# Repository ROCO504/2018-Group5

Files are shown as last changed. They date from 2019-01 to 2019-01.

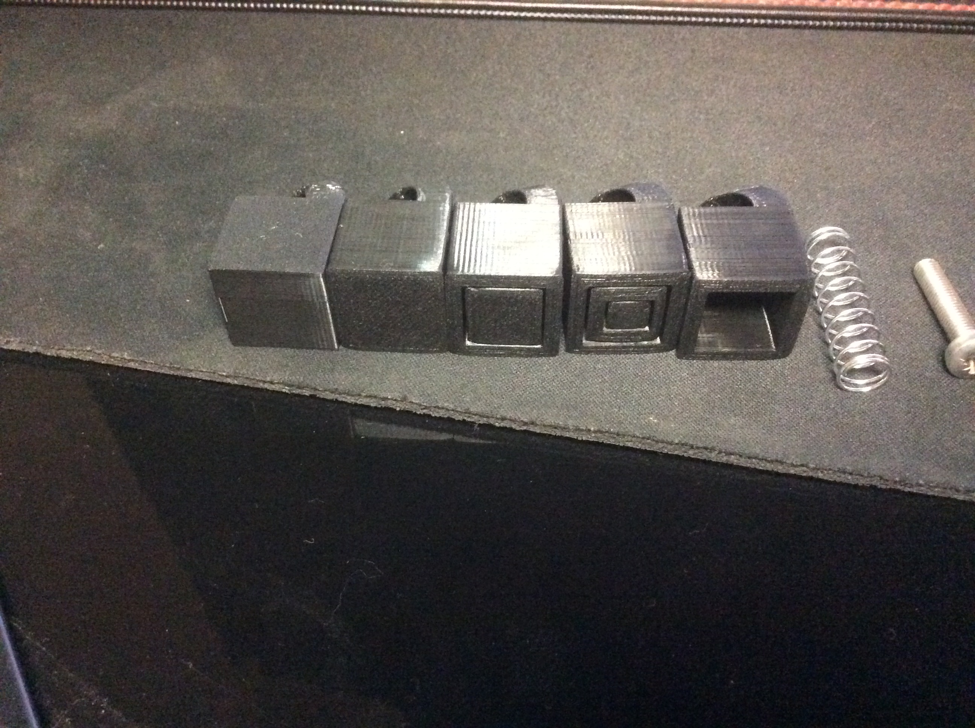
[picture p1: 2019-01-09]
Pictures/Test Cubes.JPG

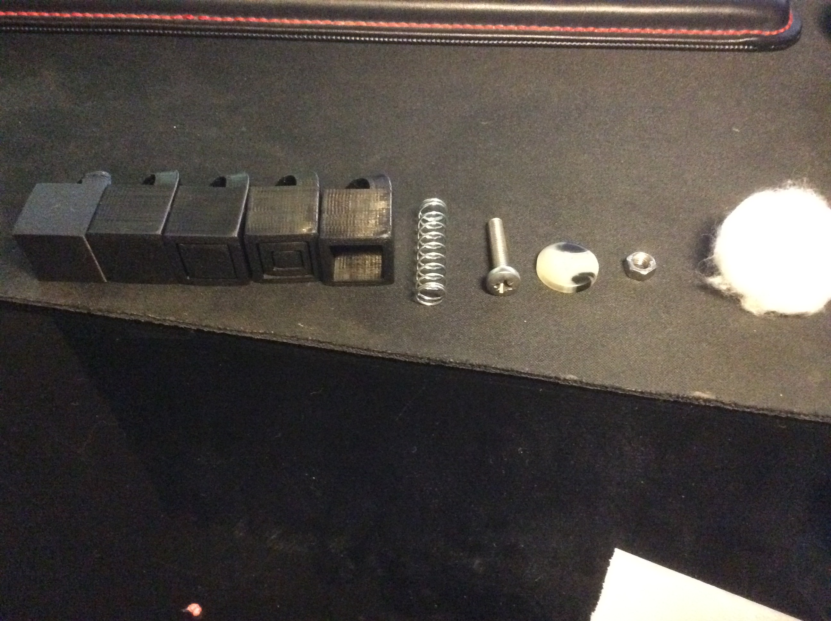
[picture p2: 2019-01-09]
Pictures/All Test parts.JPG

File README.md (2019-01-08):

ROCO504 Group 5 Readme File

Robotic Jamming gripper Hand Repository

This is a repository created for the Roco 504 module at Plymouth University in the school of Computing, Electronics and Mathematics. The code, design files and additional folders are created specifically for this project. The code is developed to be used on an Arduino Mega 2560 using 4 potentionmeters to control the digit position. 

The code is a simple digit control as the majority of this project was research based looking at the limits of using the jamming transition for grip strength

The FEA is adapted from the early design work and guided the itterations of rapid prototyping

Tensile Testing Data was gathered in the Smeaton Materials Lab.

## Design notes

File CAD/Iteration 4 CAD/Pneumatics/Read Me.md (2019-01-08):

A Store for CAD Files for parts relating to the air systems

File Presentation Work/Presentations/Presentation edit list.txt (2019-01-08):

Slide 1 TITLE
Slide 2 Why
	Hybrid/Soft/Hard
	Explain pros/cons of each
Slide 3 Project progress
	Start from comparing hard grippers, hands and human hand
Slide 4 Design key structure
	Break down into parts
		-Digit
		-Base
		-Pneumatics
			-Air vs water
			-Filter
		-Electronics
		-Code
Slide 5 Design Progression
	Digit Iterations
	Base Iterations
	Code Iterations
Slide 6 Electronic Progression
	Compare the motor strengths
Slide 7 Project Development
	Talk through what went right/wrong
Slide 8 Numerical Data of testing jamming
	Testing of different granuals vs journal articles
Slide 9 Overall design at presentation
	Picture talk about what it does

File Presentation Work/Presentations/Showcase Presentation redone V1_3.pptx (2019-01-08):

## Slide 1

Soft Jamming Robotic Gripper
An alternative approach to a compliant hand
Douglas Tilley & Liam Grazier

## Why a hybrid?

- In modern robotics, generally 3 different types of gripper are found, these are solid grippers, soft grippers and hybrid grippers.
- A brief comparison

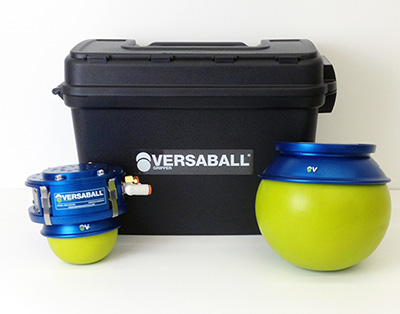
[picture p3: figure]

Solid Grippers
Pros
- Cheap
- Robust, tried design
- Predictable Behaviour
Cons
- No Compliance
- Simple
- Requires a lot of human programming and path planning
- Designed specifically for one job

Hybrid Grippers
Pros
- Often designed for multiple jobs
- Efficient
- Carry some compliance
- Predictable Behaviour
Cons
- Research based designs currently
- Expensive
- Can be unique/untested

Soft Grippers
Pros
- Compliant behaviour
Cons
- Research based designs currently
- Difficult manufacturing process
- Can often be unpredictable

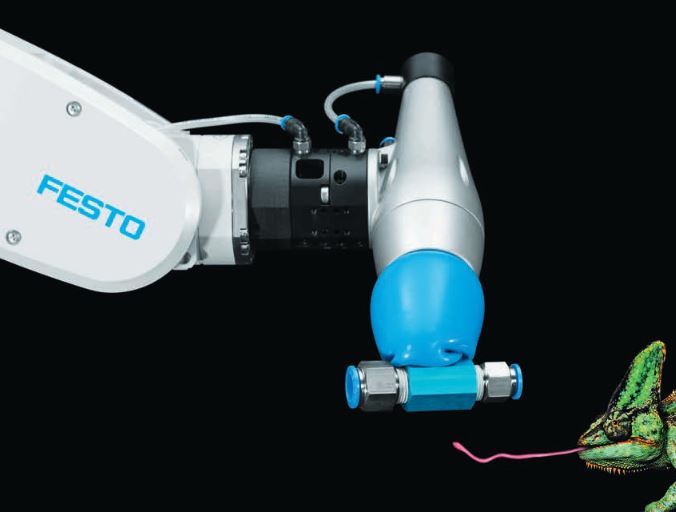
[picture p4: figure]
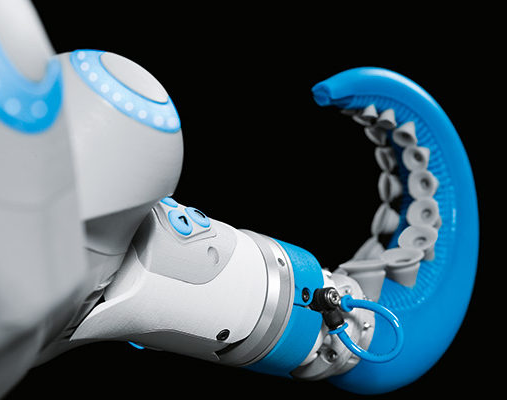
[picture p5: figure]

The point of the hybrid design of gripper is to take the compliance of a Soft robotic gripper and to combine it with the predictable behaviour of the solid gripper.
This allows for a wider range of tasks to be performed.
Festo, a US based company, has done lots of research into Soft pneumatic grippers.

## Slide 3

Project Progress:

Task | 30/09/2018 | 07/10/2018 | 14/10/2018 | 21/10/2018 | 28/10/2018 | 04/11/2018 | 11/11/2018 | 18/11/2018 | 25/11/2018 | 02/12/2018 | 09/12/2018 | 11/12/2018
Initial Project Design
Preliminary Prototype of Digit
Materials Research and Eval
Motor Research and Requisition
Electronics Development
Rapid Prototyping + Development
Final Build + Intergration of all systems

## Design key structure

The hybrid gripper is broken down into 5 main parts:-
Finger
Base
Jamming principle
Air vs Water
Filter type
Outer material
Electronics
Code
Each of these sections had their own design development

Finger
The main design choice here was how to integrate the soft jamming gripper into the finger whilst keeping the manipulation ability.
Another consideration was the modularity and link number.

Base
The base required a minimum size to be able to wrap around the objects but also it was necessary to not be too small as to cause collisions

Jamming Principle
It was necessary to do some tests into how the different materials functioned when used in the gripper.
One of the main issues here was the ability to make the system air tight.

Electronics
Motor choices, board choices, wiring methods and power consumption must be considered in this part.

Code
The code for each digit must be non-blocking to allow each finger to be controlled independently.

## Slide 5

Design progression

Over the course of this project the design has changed in various ways due to limitations and improvements found.
The rapid prototyping focus of this project meant that each part was developed and improved multiple times with the number of design iterations listed below:
Finger – 7 iterations
Starting out as a simple square and no additional features.
Added and moved the height of the tendon holes.
Posts on the back of the finger were added to give an elasticated limit.
The posts couldn’t deal with the forces exerted when 3D printed and hence were thickened.
Bases – 3 iterations
Started out as a fixed square intending to be a hand formation.
This was quickly changed to a 3 pronged design.
Had to change the base design due to motor design change.
The base was made larger and features removed for simplicity.
Pneumatic Rack – 1 iteration
Spindles – 2 iterations
Initially designed for a specific motor
Had to be adapted due to technical challenges

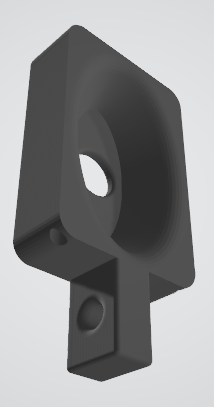
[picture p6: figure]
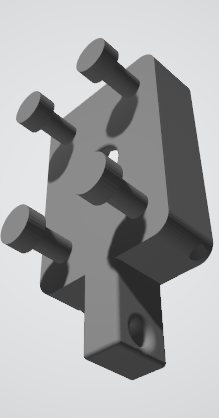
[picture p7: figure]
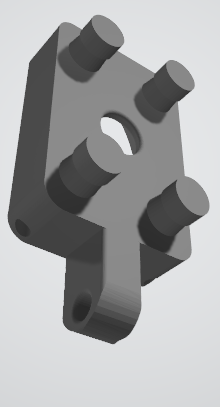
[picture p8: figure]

CAD Preview of the different iterations of designing the finger parts

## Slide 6

Electronic progression

The basis of this project was around the motors that had to be used. They had 2 tasks and each required 3 motors. This was the individual finger control and individual finger pneumatic control.
Due to various issues encountered during programming, the project changed motors 3 times.
Robotis Dynamixel MX-28
Originally this motor was intended to be used, however the motors were unresponsive to programming and hence had to be swapped out for a different stepper.
28BYJ-48 5V DC Stepper Motor
These were the second motors looked at for use in this project, using ULN2003 Chips to control the stepper motor.
However the stall torque of the motors was too low and hence couldn’t be used.
Nema17
Nema17s carry industry weight as being reliable and easy to program whilst having a reasonable stall torque.

Electronic Developments:
- Had issues controlling motors.
- Started developing low power stepper motor solution.
- Multiple Stepper Motor Controller developed for six motors.
- Three for tendon control.
- Three for crushing control.
- Issue found using 28BYJ-28 stepper motors. Not powerful enough for either task, switched out for NEMA17 Stepper motors .

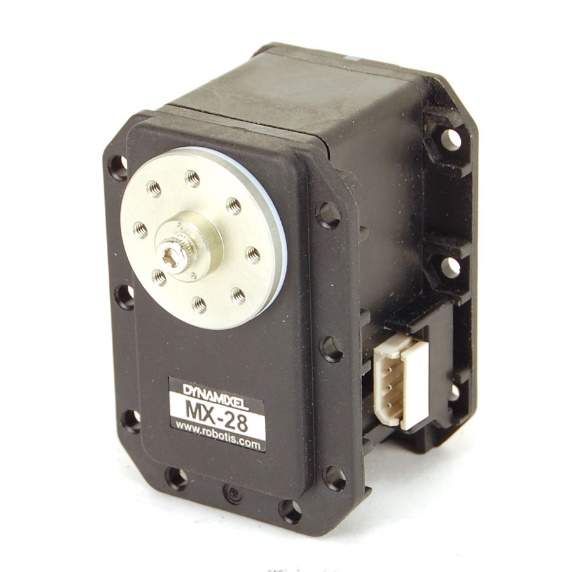
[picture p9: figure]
Image result for MX-28
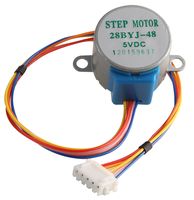
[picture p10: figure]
858 - Stepper Motor, 512 Step, 5V dc
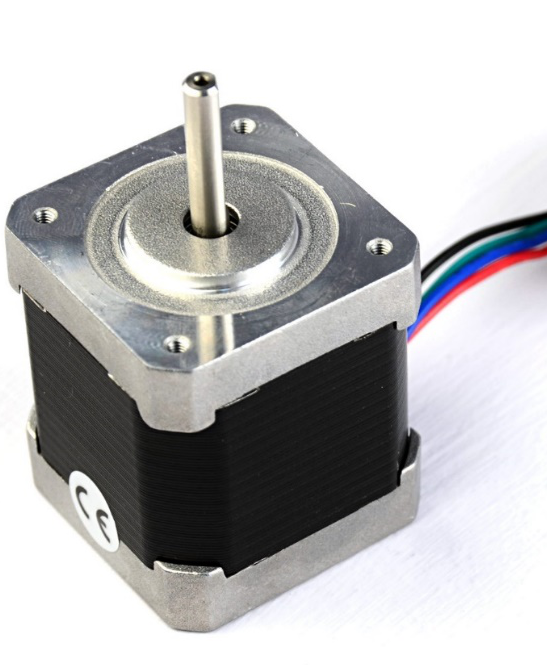
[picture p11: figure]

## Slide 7

Materials Research

To make sure that the Jamming principle worked, materials research was necessary.
A basic test right was designed to obtain some numerical data which can be shown below:

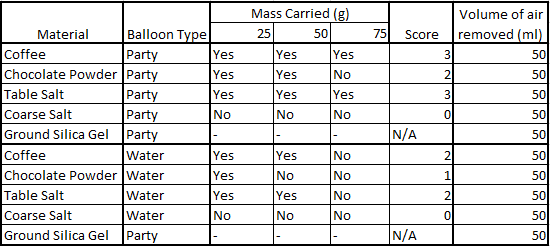
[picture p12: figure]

From this data, a scoring system was gauged and the materials choices were edited.
However, from research articles, the material that is being gripped has a large impact on the ability to grip.
A paper was conducted by Brown et al. into the shape, material and principle of the jamming gripper.
In their tests for strength and minimum contact area, a spherical object was used.

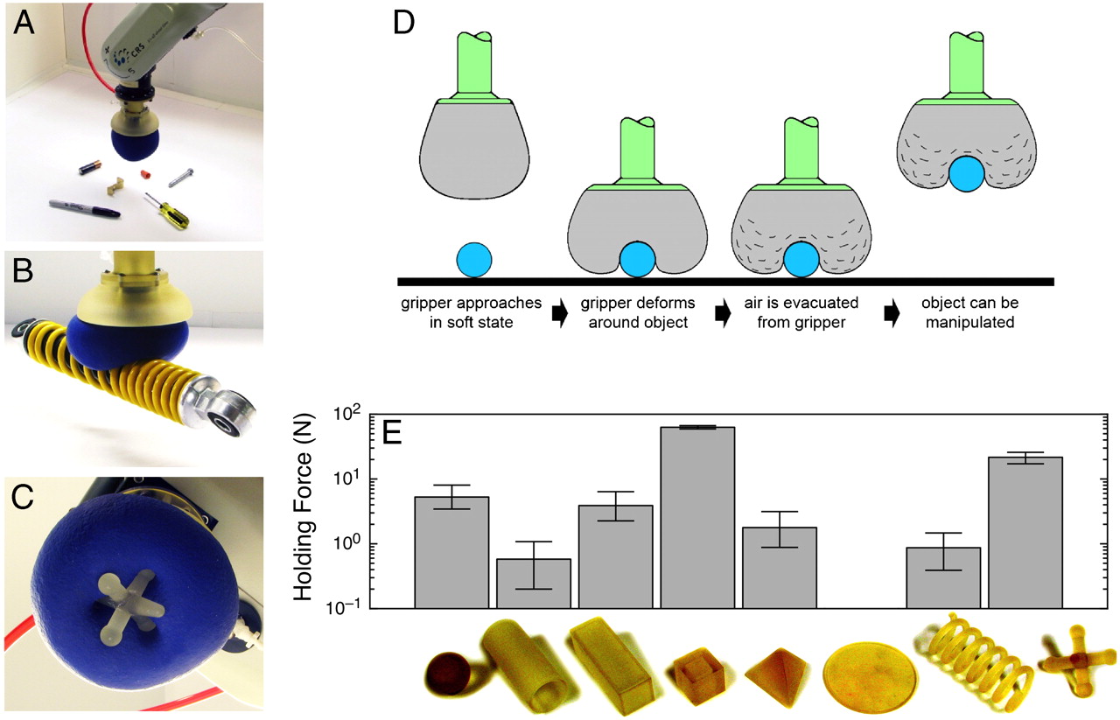
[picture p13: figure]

To conclude the packing density of the balloon matters the most whilst only a small area of the target object has to be in contact to grip.

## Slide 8

Project Development

Aims, Achievements and Future development
Aims
Individual finger control
Pneumatic Control
Ability to grip
Achievements
Individual Finger Control
Automatic Rack and Pinion Control
Some ability to grip
Future Developments
Improve the interfacing between digit and base
Make the pneumatics air tight
Reduce sizes.

Necessary changes
- Currently each finger can be position controlled, however it is a rough working with some flaws.
- The air system is not sealed correctly, however the principle works(See table). Hence the pneumatics need an overhaul.
- Friction of the syringe limits its ability due to torque issues with motors.
- Design needs to be optimized still.

Conclusion
The Soft jamming robotic gripper, when fully functional will provide added gripping ability to a traditional gripper, however getting to the stage where this works is difficult.

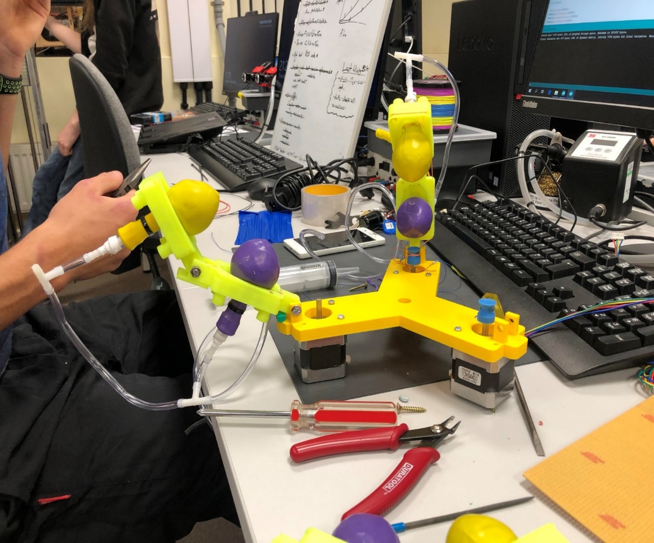
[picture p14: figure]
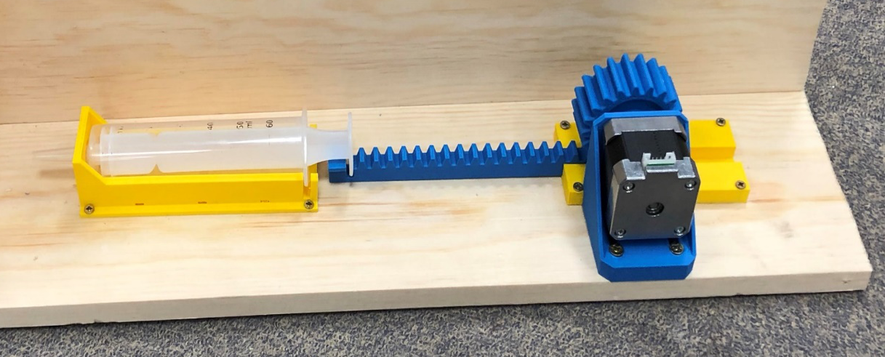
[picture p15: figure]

## References & Bibliography

Eric Brown, Nicholas Rodenberg, John Amend, Annan Mozeika, Erik Steltz, Mitchell R. Zakin, Hod Lipson, and Heinrich M. Jaeger, Universal robotic gripper based on the jamming of granular material, PNAS, 107 (44) (2010) 18809-18814; 10.1073/pnas.1003250107 (https://doi.org/10.1073/pnas.1003250107)
https (https://www.pnas.org/content/107/44/18809):// (https://www.pnas.org/content/107/44/18809)www.pnas.org/content/107/44/18809
F. Iida, C. Laschi, Soft robotics: challenges and perspectives, Procedia Comput. Sci. 7 (29) (2011) 99–102; 10.1016/j.procs.2011.12.030 (https://doi.org/10.1016/j.procs.2011.12.030)
https (https://www.sciencedirect.com/science/article/pii/S1877050911006958)://www.sciencedirect.com/science/article/pii/S1877050911006958
John R. Amend, Eric M. Brown, Nicholas Rodenberg, Heinrich M. Jaeger, and Hod Lipson, A Positive Pressure Universal Gripper Based on the Jamming of Granular Material, IEEE Transactions on robotics, 28 (2) (2012); 10.1109/TRO.2011.2171093 (https://doi.org/10.1109/TRO.2011.2171093)
https://jfi.uchicago.edu/~jaeger/group/JaegerGroupPapers/granular/TRO2171093.pdf
Nagase, Jun-ya, Shuichi Wakimoto, Toshiyuki Satoh, Norihiko Saga, and Koichi Suzumori. "Design of a variable-stiffness robotic hand using pneumatic soft rubber actuators." Smart Materials and Structures 20, no. 10 (2011): 105015.
http://iopscience.iop.org/article/10.1088/0964-1726/20/10/105015/meta

Useful Links:
https (https://www.pneumatictips.com/going-soft-on-grippers/)://www.festo.com/cms/en-gb_gb/index.htm (https://www.pneumatictips.com/going-soft-on-grippers/)
https (https://www.pneumatictips.com/going-soft-on-grippers/)://www.pneumatictips.com/going-soft-on-grippers/ (https://www.pneumatictips.com/going-soft-on-grippers/)

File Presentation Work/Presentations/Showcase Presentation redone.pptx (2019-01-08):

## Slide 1

Soft Jamming Robotic Gripper
An alternative approach to a compliant .hand
Douglas Tilley & Liam Grazier

## Why a hybrid?

- In modern robotics, generally 3 different types of gripper are found, these are solid grippers, soft grippers and hybrid grippers.
- A brief comparison

Solid Grippers
Pros
- Cheap
- Robust, tried design
- Predictable Behaviour
Cons
- No Compliance
- Simple
- Requires a lot of human programming and path planning
- Designed specifically for one job

Hybrid Grippers
Pros
- Often designed for multiple jobs
- Efficient
- Carry some compliance
- Predictable Behaviour
Cons
- Research based designs currently
- Expensive
- Can be unique/untested

Soft Grippers
Pros
- Compliant behaviour
Cons
- Research based designs currently
- Difficult manufacturing process
- Can often be unpredictable


The point of the hybrid design of gripper is to take the compliance of a Soft robotic gripper and to combine it with the predictable behaviour of the solid gripper.
This allows for a wider range of tasks to be performed.

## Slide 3

Project Progress:

Task | 30/09/2018 | 07/10/2018 | 14/10/2018 | 21/10/2018 | 28/10/2018 | 04/11/2018 | 11/11/2018 | 18/11/2018 | 25/11/2018 | 02/12/2018 | 09/12/2018 | 11/12/2018
Initial Project Design
Preliminary Prototype of Digit
Materials Research and Eval
Motor Research and Requisition
Electronics Development
Rapid Prototyping + Development
Final Build + Intergration of all systems

## Design key structure

The hybrid gripper is broken down into 5 main parts:-
Finger
Base
Jamming principle
Air vs Water
Filter type
Outer material
Electronics
Code
Each of these sections had their own design development

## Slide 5

Design progression

Over the course of this project the design has changed in various ways due to limitations and improvements found.
The rapid prototyping focus of this project meant that each part was developed and improved multiple times with the number of design iterations listed below:
Finger – 7 iterations
Starting out as a simple square and no additional features.
Added and moved the height of the tendon holes.
Posts on the back of the finger were added to give an elasticated limit.
The posts couldn’t deal with the forces exerted when 3D printed and hence were thickened.
Bases – 3 iterations
Started out as a fixed square intending to be a hand formation.
This was quickly changed to a 3 pronged design.
Had to change the base design due to motor design change.
The base was made larger and features removed for simplicity.
Pneumatic Rack – 1 iteration
Spindles – 2 iterations
Initially designed for a specific motor
Had to be adapted due to technical challenges


CAD Preview of the different iterations of designing the finger parts

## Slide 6

Electronic progression

The basis of this project was around the motors that had to be used. They had 2 tasks and each required 3 motors. This was the individual finger control and individual finger pneumatic control.
Due to various issues encountered during programming, the project changed motors 3 times.
Robotis Dynamixel MX-28
Originally this motor was intended to be used, however the motors were unresponsive to programming and hence had to be swapped out for a different stepper.
28BYJ-48 5V DC Stepper Motor
These were the second motors looked at for use in this project, using ULN2003 Chips to control the stepper motor.
However the stall torque of the motors was too low and hence couldn’t be used.
Nema17
Nema17s carry industry weight as being reliable and easy to program whilst having a reasonable stall torque.

Electronic Developments:
- Had issues controlling motors.
- Started developing low power stepper motor solution.
- Multiple Stepper Motor Controller developed for six motors.
- Three for tendon control.
- Three for crushing control.
- Issue found using 28BYJ-28 stepper motors. Not powerful enough for either task, switched out for NEMA17 Stepper motors .

Image result for MX-28
858 - Stepper Motor, 512 Step, 5V dc

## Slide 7

Project Development

Aims, Achievements and Future development
Aims
Individual finger control
Pneumatic Control
Ability to grip
Achievements
Individual Finger Control
Automatic Rack and Pinion Control
Some ability to grip
Future Developments
Improve the interfacing between digit and base
Make the pneumatics air tight
Reduce sizes.

Necessary changes
- Currently each finger can be position controlled, however it is a rough working with some flaws.
- The air system is not sealed correctly, however the principle works(See table). Hence the pneumatics need an overhaul.
- Friction of the syringe limits its ability due to torque issues with motors.
- Design needs to be optimized still.

Conclusion
The Soft jamming robotic gripper, when fully functional will provide added gripping ability to a traditional gripper, however getting to the stage where this works is difficult.

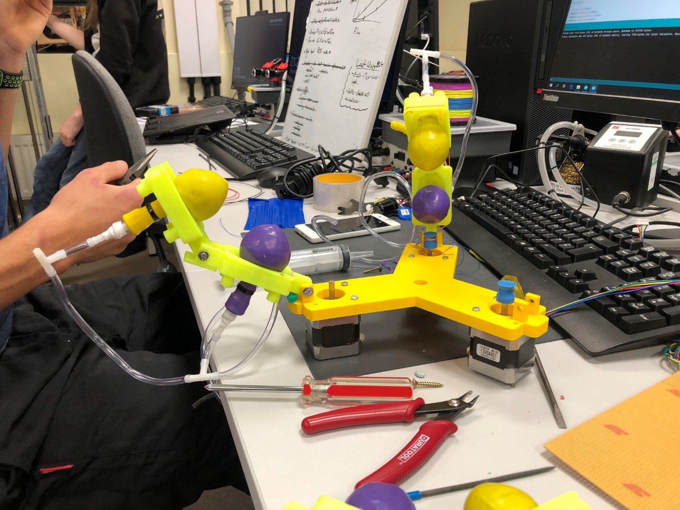
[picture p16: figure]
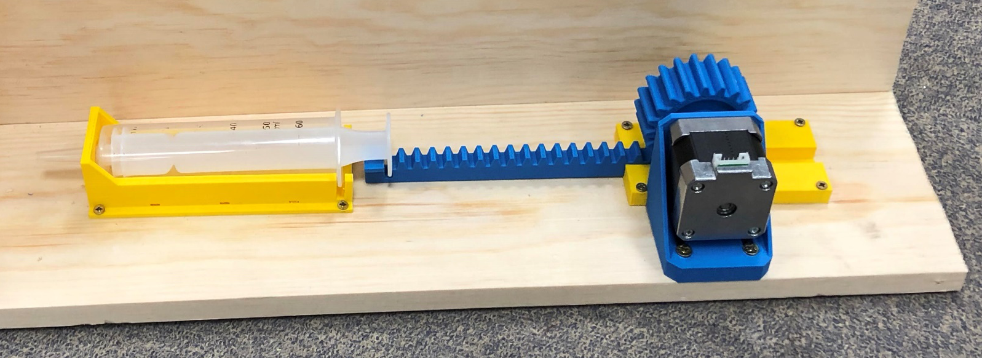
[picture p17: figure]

## Some references for now

- https://www.pneumatictips.com/going-soft-on-grippers/
- https://www.sciencedirect.com/science/article/pii/S1877050911006958
- https://jfi.uchicago.edu/~jaeger/group/JaegerGroupPapers/granular/TRO2171093.pdf

- https://www.pnas.org/content/107/44/18809

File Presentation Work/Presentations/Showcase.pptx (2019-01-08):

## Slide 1

Soft Jamming Robotic Gripper
An alternative approach to a compliant .hand
Douglas Tilley & Liam Grazier

## Why a hybrid?

- Traditional grippers

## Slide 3

Project Progress:

Task | 30/09/2018 | 07/10/2018 | 14/10/2018 | 21/10/2018 | 28/10/2018 | 04/11/2018 | 11/11/2018 | 18/11/2018 | 25/11/2018 | 02/12/2018 | 09/12/2018 | 11/12/2018
Initial Project Design
Preliminary Prototype of Digit
Materials Research and Eval
Motor Research and Requisition
Electronics Development
Rapid Prototyping + Development
Final Build + Intergration of all systems

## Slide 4

Design Developments:

Finger development
- 2 link vs 3 link
  - It was found that through rapid prototyping that using 3 links caused collision conflicts.
  - The torque required by the motors to control 3 links was too much, whilst with 2 links it was actuatable.
  - 3 links caused over rotation of the joint and hence without it was not possible to return the digit to the original position without another motor.2 link vs 3 link
- asda
- 2 link vs 3 link

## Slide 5

Prototype Developments:

The main developments from stage 1 of the design was adding rear posts to allow an elastic recoil.
Stage two added posts that were functional, but sadly not strong enough.
Stage three saw stronger posts added to the rear, these were much more suitable for this project

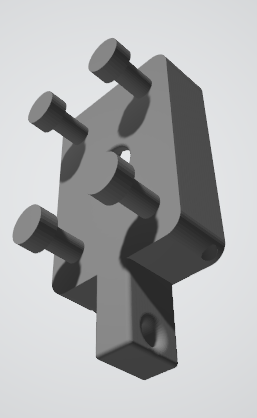
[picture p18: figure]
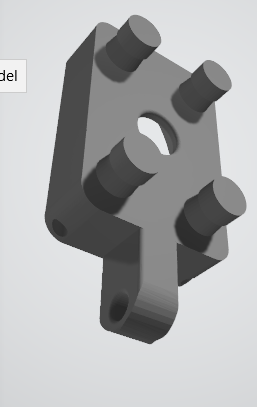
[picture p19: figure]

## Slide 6

Electronic Developments:
- Initially started using the MX-28
- Developed RS-485 Circuit
- Had issues controlling motors
- Started developing low power stepper motor solution.
- Multiple Stepper Motor Controller developed for six motors
- Three for tendon control
- Three for crushing control
- Issue found using 28BYJ-28 stepper motors. Not powerful enough for either task, switched out for NEMA17 Stepper motors

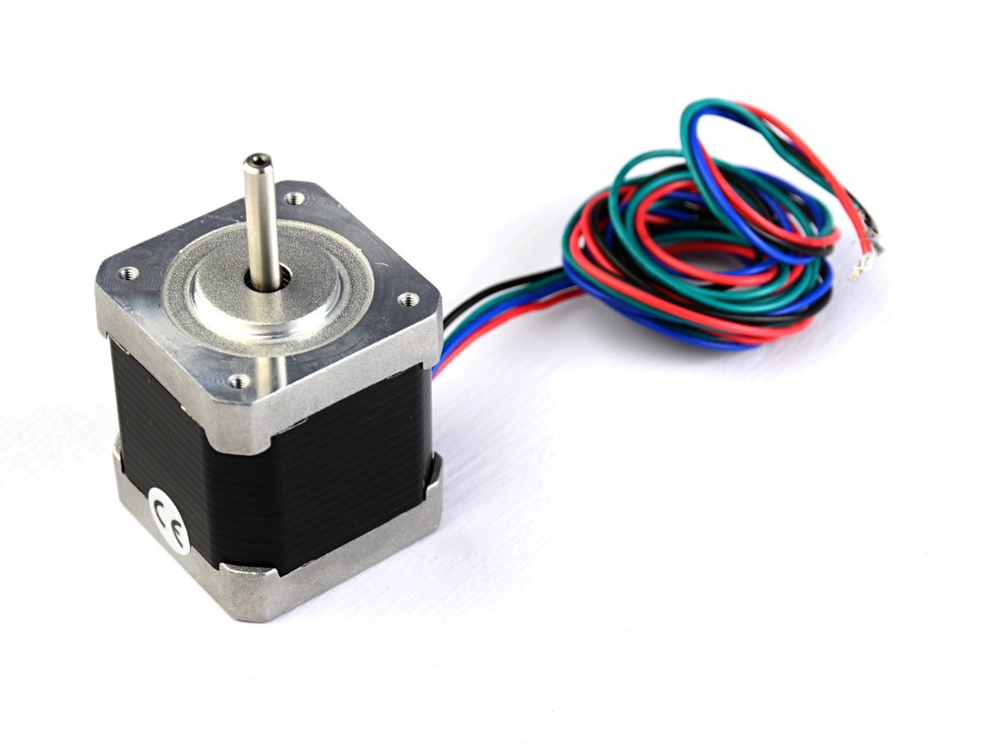
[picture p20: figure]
858 - Stepper Motor, 512 Step, 5V dc
Image result for MX-28

## Project Development

Automated Syringe rack gearbox working, but due to low
Strength of the motors, there is not enough torque for the syringe
To draw air.
This would require a higher torque motor.
The prototype is on display. All the parts are ready for
Implementation upon purchase of higher strength motors.
The gripper has been reworked to integrate the NEMA 17s onto a new
Base plate. Old prototypes can be seen on the work bench.
Rapid prototyping using technologies such as 3D Printing, and laser cutting
All fuelled by CAD/CAM software, there has been many iterations of parts.
Digit (Singular Part) – 6
Bases (Singular Part) – 2
Pneumatic Rack (5 Part Assembly) – 1
Spindles (Singular Part) – 2


## Prototype Testing

## Code Developments

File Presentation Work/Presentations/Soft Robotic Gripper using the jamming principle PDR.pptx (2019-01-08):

## Soft Robotic Gripper using the jamming principle

Preliminary Design Review

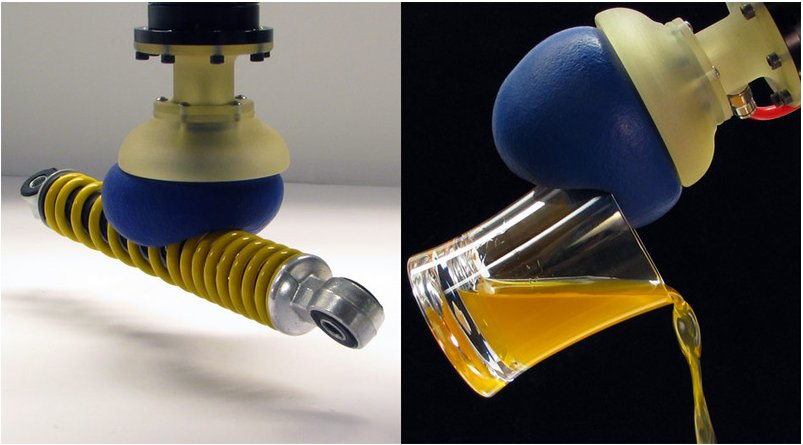
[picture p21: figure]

http://www.hizook.com/files/users/3/Jamming_Robot_Hand_2.jpg

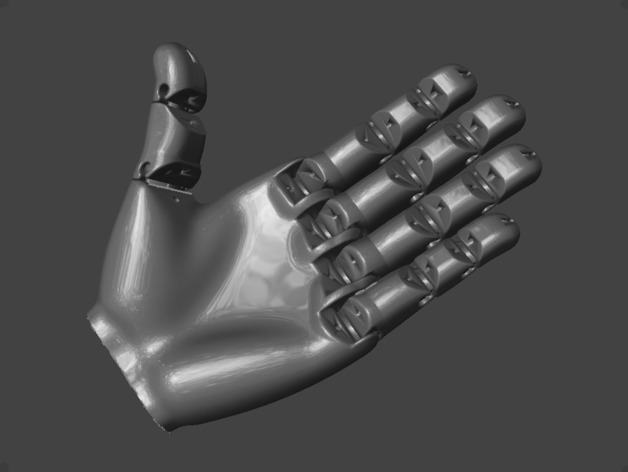
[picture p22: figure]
A picture containing indoor Description generated with high confidence

https://www.thingiverse.com/thing:242639

## Key Points of the Soft Gripper

- Uses the Jamming principle.
- Multiple Joints for points of contact
- Tendon control for actuation of the gripper
- Vacuum Control

## Jamming Principle Key points

- Various different particles work in different ways
- Due to Crystalline structures varying.
- The size of the particles has an effect on how easy to form around the gripper and hence strength of the grip.
- Due to the small sizes a vacuum is needed to form a strong vacuum.

## Different Particle Considerations

Some of these considerations are found in Jamming of Soft Particles: Geometry, Mechanics, Scaling and Isostaticity (van Hecke, 2010)
- There are a variety of different particles considered in building:
  - Salt(Size grades 1-4[Found on salt grinders])
  - Coffee
  - Chocolate Powder
  - Flour
  - Silica Gel
- Vacuum Method.
  - Cotton as a clog
  - Cheese Cloth
  - Tissue paper

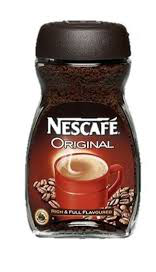
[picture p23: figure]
Image result for coffee granules
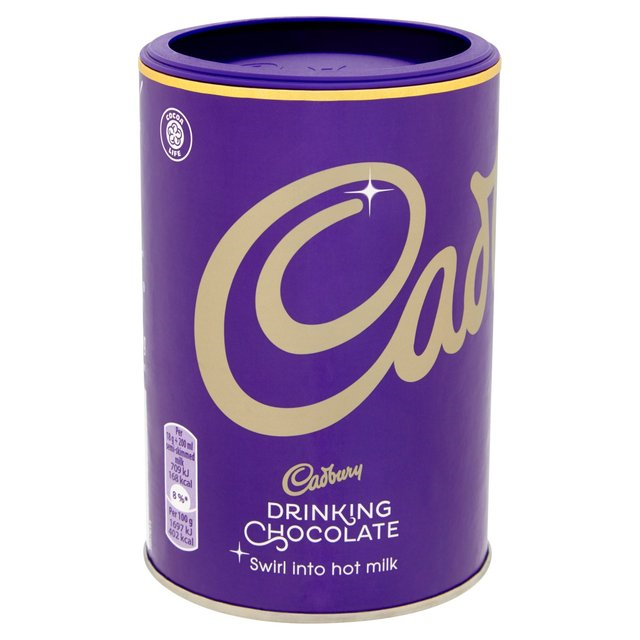
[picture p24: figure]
Image result for hot chocolate cadbury
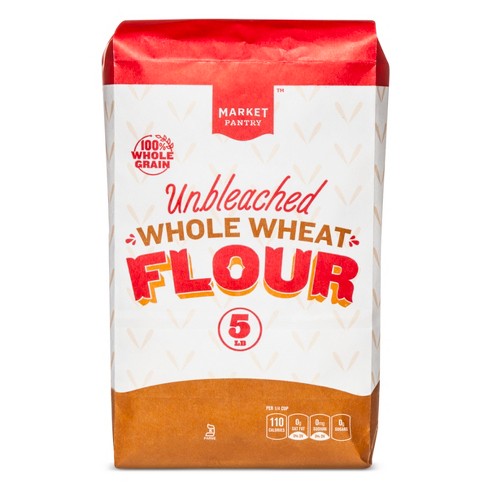
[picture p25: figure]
Image result for flour
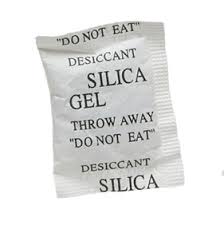
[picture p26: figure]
Related image

## Design Considerations

- How is the control of the multiple joints implemented.
- How to control the Vacuum?
- Gripper size considerations.

## Prototyping

- Design considerations:
  - Potentially using a central bone with balloon around the outside.
  - Using a flat surface with the balloon inside.
- Critical Evaluation:
  - The design only focuses on open and closed.
  - Just a singular digit for now to show principle design.
  - No pressure sensor to halt the motion and activate the gripper vacuum(at this stage).

## Preliminary Findings.

- It was found that with low vacuum pressure, slightly larger particulate matter is better.
- When using low vacuum pressure it is best to wrap the whole object
- Cotton wool works sufficiently as a block
- Re-arrangement of particles is useful but not necessary

## Journals & Credits

- van Hecke, M. . Jamming of Soft Particles: Geometry, Mechanics, Scaling and Isostaticity. Journal of physics. Condensed matter : an Institute of Physics journal. 22. 033101; DOI: 10.1088/0953-8984/22/3/033101.
- Eric Brown, Nicholas Rodenberg, John Amend, Annan Mozeika, Erik Steltz, Mitchell R. Zakin, Hod Lipson, Heinrich M. Universal robotic gripper based on the jamming of granular material. Jaeger Proceedings of the National Academy of Sciences Nov 2010, 107 (44) 18809-18814; DOI: 10.1073/pnas.1003250107
- Y. Li, Y. Chen, Y. Yang and Y. Wei, "Passive Particle Jamming and Its Stiffening of Soft Robotic Grippers," in IEEE Transactions on Robotics, vol. 33, no. 2, pp. 446-455, April 2017. doi: 10.1109/TRO.2016.2636899
- http://www.physics.emory.edu/faculty/weeks/lab/papers/sendai2007.pdf

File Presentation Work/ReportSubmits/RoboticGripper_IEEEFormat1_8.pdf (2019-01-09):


NO DOI, ROCO 504 ©2019 IEEE

# Compliant gripper Using the Jamming principle

Douglas J. Tilley
School of Computing, Electronics and Mathematics,
Plymouth University,
UK
douglas.tilley@students.plymouth.ac.u k

Liam Grazier
School of Computing, Electronics and Mathematics,
Plymouth University
UK
liam.grazier@students.plymouth.ac.uk

Martin Stoelen
Fieldwork Robotics ltd
Plymouth,
UK
martin.stoelen@plymouth.ac.uk

Abstract—Traditional robotic grippers focus on using control electronics to limit motion and stop crushing. However, in recent years soft compliance has started to take over to reduce the pressure on accuracy. There are very few grippers that have incorporated hard and soft elements of the gripper. Where this is used, soft tendons are the primary method. In this paper, we attempt to mimic the soft pads of the human hand and apply the particulate jamming transition in them to gain grip. 3D printed Polylactic acid (PLA) was used to make the gripper whilst due to the nature of jamming, multiple particles had to be tested. (Abstract)

Keywords—Robotic | gripper, | Jamming, | Soft | robotics,
grasping.
I. INTRODUCTION
Gripping various abstract objects is a task that comes naturally to the human hand and is a passive task we perform that is very often overlooked. Whilst this is the case for a human, for a robot gripping is a complex task requiring positional awareness and attaining the correct grip strength to not crush the object. This has led to an ever-expanding sector of soft robotics looking at different elements of compliance, favoured mainly by the bio-inspired tendons in the hand [1]. Regarded as an evolutionary success, seen in various animals, this tendon design allows for both underactuated manipulators and for complex control to be developed looking at the motion of the hand. Although the tendons provide precise control and a small bit of compliance, potential slip of an object is still a problem that exists. This is traditionally solved using a surface with high contact friction or by using protrusions of an object to wrap around.
The aim of this paper is to investigate applying multiple soft elements of robotics into a hard-robotic gripper, something that is not often done [2]. This is in hope of further development to help create a universal gripper that can be applied to robots in working environments alongside humans. Competitions have been set out to look at this principle of a universal gripper, however none have achieved it to the same degree a human can. The development and research of this device looks to help progress along this path.
The jamming phase transition is used to describe the range of phenomena shown by granular and viscous liquids to change between states [3] [4]. This complex behavior of materials is commonly supported by a jamming phase diagram which can be seen in Figure 1 The jamming phase diagram by Liu and Nagel . This shows the ability for jammed materials to support a load. This jamming transition has been described to use three independent variables: packing fraction, a functional temperature and pressure. If one of the variables is not sufficient the phase transition does not occur. However, it is through this phase transition that elements of both soft and hard robotics can be used. To satisfy the needs of a universal gripper a hybrid approach must be taken to allow precise grip at the end of the digits whilst maintaining the broad ability of a traditional gripper. To combat the problem of traditional jamming grippers having to apply force from a direction onto the target object, this gripper uses multiple contact points, then the jamming transition is applied. This allows traditional gripping means to be used and hence compatible with previous generations for grippers, however it adds the grip that is obtained through the jamming and hence for tasks that occasionally have gripping failure, allows higher success rates.

II. SIMILAR AND RELEVANT WORK
There is an increasing number of researchers looking into use of the jamming transition in soft robotics due to the compliance it allows [6] [7] [8] [9] [10].
There are similar works that look at the use of the jamming transition to fix the position of the joint. Although some grippers have been developed as a single soft object to wrap around a target. These grippers still encounter issues when an object cannot find an edge, or it cannot be wrapped around [6] [7].
Although typically anthropomorphic designs use independent control of each joint. It is still an active area for research which companies, such as DLR, are designing upper limbs and hands. However, there is also research into underactuation with limited control providing complex motion [11] [12] [13]. The underactuation allows for the actuator to be placed in either the hand or wrist to allow for the joints to be slimmer and hence gain added control [14]. This also allows for a smaller and lighter design as the

Figure 1 The jamming phase diagram by Liu and Nagel [5]

actuation can be moved away from the end effector. Examples of this tendon driven design include the i-HY hand design, [15] the multi-fingered Robotic Hand by Mizushima et al [16] and the Meka M² Gripper [17]. This is a popular design which focuses on attaching a tendon to the finger link and then the joint is rotated through the pulling of this tendon.
Although tendon control is commonly used, there is still large funding and resources going into mechanical designs for robotic grippers. This is shown by the production of the SARAH gripper for use on the ISS [18].
Ying Wei et al. in their paper “A Novel, Variable Stiffness Robotic Gripper Based on Integrated Soft Actuating and Particle Jamming” [19] show that there is a desire for abstract designs to be developed over traditional designs. In the paper they looked at using the jamming principle for a similar purpose to mimic adding grip to the digit. However, the principle used in this paper is to use completely soft elements as the spine of the design and it is using air actuation instead of traditional gripper designs. It was shown that using the jamming transition provided an improvement in grip which led to further the designs looking at passive jamming [20]. However, Ying wei et al. in this paper ended up going with the soft design completely.
Another application for the jamming transition in grippers is to lock the digit in place. This was investigated by Mizushima et al. using a soft rubber sleeve and a large granular material, which in this case was rice [16]. Numerical data was gathered, and they found that using small granular material for stiffness jamming was not as good as using larger grains such as rice. This is contrary to the Topical review conducted by M. van Hecke where it was discussed that as the grain size was increased, the grip strength exerted through the jamming transition was lower [21].

III. DESIGN PROCESS AND ANALYSIS
Due to the nature of keeping the gripper linear in a similar manner to a human digit, it means that the primary method used in many tendon-controlled grippers cannot be used [22]. This is due to the primary means of control being a single linear tendon down the middle of the digit. However, the primary design principle is keeping the middle of the digit free to allow for a vacuum pump to be used. Given sufficient resources this could be adapted with specifically built granular packs to allow for a small vacuum pipe to be used. This could be then made linear in-line with the tendons, simplifying the design. However, the design addressed in this paper was based around this principle of avoiding the middle of the digit to allow space for the vacuums to be attached to the granular packs.
For deciding the material of the granular packs, a short unscientifically valid study was conducted on various materials. It was found that the use of Coffee or table salt were the best options. These findings were supported by Liu and Nagel [5]. However due to common use of coffee in jamming transition grippers it was decided to use this to keep the results comparable to other studies [6] [7]. An important point to note is the lower density of Coffee provides an overall reduced weight to the gripper head [7].

Rapid prototyping was conducted using computer aided design (CAD) and computer added manufacture (CAM) using fused filament fabrication (FFF) printing, commonly known as Fused Deposition Modelling (FDM). This meant that logical steps could be taken to improve on each design as problems were encountered. When used in combination with a logical design process it can help to speed up design to allow for additional data to be gathered.

A. Finite Element Analysis (FEA)
When some of the parts were tested in a real environment it was found that they were breaking in certain areas repeatedly and hence FEA was performed to analyse why this was happening. FEA can be used to gauge the strength of a design and find weak points. Although FEA is a powerful engineering tool for finding weaknesses it is hard to accurately model FFF printing as the method of construction changes the properties drastically. This is due to the strength of the print varying depending on which axis the FFF printing is done from. This alongside temperature and the composition of the filament make performing FEA in CAD difficult. Hence to form an algorithm to perform FEA, the strength of the bonds between each layer must be examined.

Polylactic acid (PLA) is a common material used for rapid prototyping and 3D printing. However, it can be found that the performance of FEA is questionable and that some of the results found in one direction are not valid in another. Hence in common CAD software, such as Solidworks and Fusion 360, the material is not found in the materials database and hence properties must be assumed or become a collage of multiple different data sets. In real application, it can be found that plastic deformation will occur in the stressed parts of a 3D printed design. This can be addressed partly by increasing the infill of the parts or reducing the layer height. But this will directly affect the print time. Table 1 shows print times of the initial digit iteration 1 with the changing of the infill and the layer height. Although, as a rough outline Acrylonitrile butadiene styrene (ABS) can be used to simulate PLA poorly, though to solve this issue a new orthotropic material must be created [23]. There is a lack of information about the topic of PLA, however research is being conducted to find out the material properties of different PLAs [24] [25] [26]. In the case of this paper, an isotropic material is assumed for simplicities sake as the FFF connection strength between the layers of the extrusion cannot be found.

Table 1 Print time comparisons between layer height and infill

Layer Height | Infill | Print Time | Layer Height | Infill | Print Time
0.1 | 10% | 3H10Min | 0.2 | 10% | 1H35Min
0.1 | 20% | 3H34Min | 0.2 | 20% | 1H47Min
0.1 | 30% | 4H02Min | 0.2 | 30% | 2H01Min
0.1 | 40% | 4H25Min | 0.2 | 40% | 2H13Min
0.1 | 50% | 4H49Min | 0.2 | 50% | 2H24Min
0.1 | 60% | 5H11Min | 0.2 | 60% | 2H36Min
0.1 | 70% | 5H32Min | 0.2 | 70% | 2H47Min
0.1 | 80% | 5H53Min | 0.2 | 80% | 2H57Min
0.1 | 90% | 6H15Min | 0.2 | 90% | 3H08Min
0.1 | 100% | 8H21Min | 0.2 | 100% | 4H12Min

The variability in connection strength depends on a minimum of 5 factors: material, print temperature, room temperature, room humidity and cooling ability [24]. To keep the calculation simple ABS material properties were used as a Prusa I3 3D Printer could be loaded with ABS filament and printed with full infill to closely mimic the FEA Modelling. The results from this FEA will not be completely accurate due to the layering that occurs in FFF printing. However, this process gives a rough overview of how the design will perform.


Figure 2 displays the initial iteration of the elastic posts on the reverse side of the digits. Upon manufacturing the part using FFF; the posts were exhibited to show fragile behavior and displayed a flexible movement where the part should have been rigid. FEA for torque forces showed how a rotational force would affect the post, in Figure 2 the forces act entirely on the top of the post. Figure 2 Figure 3
Thickened elastic antagonist anchorsshows the upgraded post,
where the force exerted is spread downwards and forms a


secure connection to the base. Overall, the design of the project went through multiple design steps to reach its final iteration. This was due to gradual progression from rapid prototyping. The main progression was the improvement from static pivots to rotating pivots. It was found that the static pivots provided too much resistance to the rotation of the digit. A progression of all the middle digits can be seen in Figure 4.

B. Tensile Testing
The tendon used to retract the digit assembly is required to be strong whilst displaying some elastic properties to add compliance to the design. This increases the impact resistance of the design as the tendon stretches instead of snapping. Figure 5 shows the agonist tendon and how it runs through the digit assembly. This was based largely off the design from the M² gripper [17].


Each samples result was plotted and collated into Figure 6 and Figure 7. The elastic and plastic deformation regions are the parts that are of interest. The graphs helped to determine the material to use for each tendon.


A summary of the data for each material is shown in Table 2 which displays the numerical data displayed in Figure 6 and Figure 7.

Table 2 shows that the candidates for the agonist tendon are Nylon, Fishing Line and Flexible PLA. Each material exhibits a large elastic deformation with high load force, this allows for the agonist tendon to drive the digit assembly with high torque and not run the risk of plastic deformation.

Figure 2 FEA of the elastic antagonist of the joint

Figure 3 Thickened elastic antagonist anchors

Figure 4 Iterations of the middle link design

Figure 5 Graphical representation of the agonist(red)-antagonist(green) nature

Figure 6 Tensile test results for PLA, Nylon and Fishing line

Figure 7 Tensile test results for flexible PLA and elastic rope

Whilst for the antagonist joint the elastic 2mm thick material and the flexible PLA are suitable. Each material shows a clear elastic deformation before a sudden fracture. Flexible PLA, according to the tensile test, will be better as the antagonist due to the high ultimate tensile strength, and short displacement.

IV. TESTING
The jamming transition is the process of granular material locking its structure when a pressure difference is applied in a closed environment [27]. Unfortunately, due to the experimental set up, the pressure difference in the jamming transition is small.

A few assumptions were made at the beginning of the granular packing experiment. For the experiment it was assumed that the room was at a normal dry room temperature of 20°C with an atmospheric pressure of 101,325 Pa. The density of coffee was assumed to be 0.561g/cm³
and there was an 80% removal of air from the balloons with the assumed gas constant of 8.314J mol⁻¹ K⁻¹ Hence the volume of air in the balloon was calculated. The balloon was a uniform radial sphere of 2.25cm. All values in calculation were exact, however in display 3 significant figures was used.

Vball=

4
3

π2.25³
=47.7cm³
(1)

VCoff=

15
0.561 =26.7cm³
(2)

∴Vair=Vball-VCoff=21.0cm³
(3)

∴Vair=21.0×10⁻⁶
=2.1e

-5

cm³
(4)

Using the ideal gas law.

PV=nRT | (5)
(PChange)×(Vair × 0.80)=n ×R ×T | (6)

(PChange)×(2.1e
-5 × 1.20)=1 ×8.314 ×21 | (7)

PChange=

8.314×21
2.1e
-5 × 1.20 | (8)
PChange=69.4kPa | (9)

This is a value that when compared to a paper conducted by
T. S. Majdamur et al. a pressure difference of one and a half times provides an isostatic value of 3.5, [27] in this case the calculated number of contacts between particles, which is a significant increase from its original non-jammed value of 2.5 [21]. This value is 10kPa less than the value calculated by Eric Brown et al. where 80kPa was used for the pressure difference for jamming [6]. Whilst their findings also suggest that the jamming transition is a reversible mechanism and that by releasing the vacuum and having no stimulation the pack can still be manipulated. Although only roughly examined, the difference between an unjumbled granular pack against a jumbled granular pack was noticeable. Hence to keep the results accurate, the granular packs were jumbled randomly between each test.

Two main experiments were conducted through the design process, these were to decide on the granular material used in packing and to test the grip strength of the granular pack. Testing the grip strength of varying shapes was tested through use of a force meter pulling on the test shape. Each of the edge test shapes was made to be a cube of 20mm x 20mm x 20mm. The experimental data has been displayed

in Figure 8.; Force (N)

Figure 8 Comparing grip strengths compared to their shape


It was possible to gather some interesting results that agree with some similar papers [6] [16]. The results gathered in this paper support the hypothesis that the ability to grasp an object depended on its contact area and the grip strength [7]. As it can be seen in Figure 8, there was a large disparity in the ability to grip certain objects. One of the interesting points to note is that difference in the orientation of the PLA test parts influences the ability to grip. Although the 0 Edges and the rotated object were the same shape, there was a 500% increase in the ability for the object to be gripped.

This supports the hypothesis that if the object is wrapped around, that the grip strength will drastically increase [7]. It was also noted that the smaller objects such as the screw and the 6mm nut could not be gripped easily. This was perhaps caused by the crude experimental set up applying a directional force to the object being tested.

Sample | Maximum Force (KN) | Displacement at Maximum Force (mm) | Maximum Displacement (mm) | Force at Break (Standard) (KN)
Elastic 2mm | 0.03 | 245.1 | 262.81 | 0.01
Flexible PLA | 0.06 | 117.6 | 119.63 | 0.06
PLA | 0.15 | 28.59 | 30.87 | 0.14
Fishing Line | 0.15 | 2 | 4.73 | 0.13
Nylon | 0.14 | 5.67 | 6.6 | 0.07

Figure 9 Displaying the different test shapes

Table 2 Different Material Properties found using tensile testing

From experimental results it was possible to see the success of the grip depending on the contact percentage. The results gathered in Figure 8 were only from successful attempts to grip apart from the 6mm nut which was not possible to grip at all.


The experimental set up that is seen in was used. Of the 40 results obtained there was a 70% success rate with 2 anomalous results which suggests that the results obtained are like findings by Amend et al. [7].

The second experimental set up was examining the effects that removing volumes of air had on the grip strength. This was conducted using a syringe to gauge volume of air removed. This is shown in Figure 11, which shows an increasing trend in the grip ability as air is removed. This is in line with the results found by Amend et al. [7] such that an increase in pressure influences the ability to grip.

Force (N); Volume of air vacated (ml)

Figure 11 Grip strength compared to air vacated

The two experiments show that the jamming transition functions even at low pressure differences that and that it is not required to have a high actuation force. These results are parallel with the results found when the use of two digits around an object. This is potentially due to the hemispherical soft pads on the end of the finger [28] [29].

Although this data has been gathered, due to the limitations in testing apparatus it was not possible to form a complete vacuum and hence the full experiment was not possible. Previous studies on the pressure differences required for the jamming transition to be high pressure (600KPa+ [7]) whilst there have been few articles that look at the ability for the jamming transition to work at low pressure values.

A short study on the effect of combining the use of tendons and jamming transition was conducted. However, it returned inconclusive results with high variability. It was possibly due to the limitations in the parts used.

V. CONCLUSION
This paper has addressed the design and testing of a universal jamming transition gripper. There have been very few hard and soft robotic gripper hybrids with even less experimental results. This is in part caused by the difficulty of getting valid experimental data on grip strength due to the inherent chaotic nature of jamming. The difference of grip depending on the contact surface varies greatly. Hence to validate the results a large data pool is required suggesting a better repeatable experimental set up is required. Whilst the a relatively primitive experimental set up was used, it was possible to obtain valid data, that is supported by other periodicals and journals. The current limitations in data analysis and progression are due to limitations in manufacturing facilities and testing methods.

The elements of design displayed in this paper were a combination of factors that are still being researched; the underactuation of a robotic gripper, the jamming transition and manufacture of a universal gripper. The applications for this combination have not been thoroughly explored as soft robotics is an expanding area of research. This design is a prototype requiring further development but through the experimental data it is possible to infer that the principle works. Through the combination of the soft and the hard-robotic elements, it allows for adaptations to current designs in manufacture and with some of the findings regarding soft pads on the end of fingers supporting this. The jamming transition is a suitable technology to use in soft robotics but the ability to form a vacuum is the main limiting factor, especially in this situation. The development has covered low pressure jamming transition which has some support, but the best results have been shown at to be at high pressure differences, reaching up to ten times the values used in this paper.

VI. FURTHER DEVELOPMENT

Due to resource constraints, there are several changes that can be theorized but not implemented. This will be adapted in future iterations to deal with the problems. The primary area for improvement is the vacuum and particle pack system. The use of balloons as a proof of concept works, however using the balloons in the long run is not a suitable solution. This is due to the lack of air tight seal, the clogging of the filter and the ability for the coffee granules to reach outside the circumference of the digit bowl. In future, a specially designed particle pack will be used. Firstly, this will provide the ability to use a traditional tendon gripper design, simplifying the whole structure and reducing the strength of the actuator required. Furthermore, this means that the particle pack can be placed on top of the digit to be bio-mimetic of the human hand. Whilst similarly, irregular shaped surfaces may be used to gain further grip in the system. This will not only make the digit thinner, but it will allow the end digit to be a more familiar shape and make path planning simpler. This leads onto simplifying the

Figure 10 Experimental set up for testing grip strength tendon design back to a singular tendon to lower the actuation required for moving the digit.

As shown by calculations, the pressure difference that is possible is much lower than that of an industrial vacuum pump. Hence in future iterations a stronger vacuum will be used. The jamming transition is already beginning to see application in various fields being researched for movement and for irregular gripper designs. According to the jamming phase diagram by adding extra to one of the key elements of the jamming transition it is possible to increase the grip strength of a normal gripper and hence a pathway to commercialization.

VII. WORKS CITED

[1] E. Mattar, "A survey of bio-inspired robotics hands implementation: New directions in dexterous manipulation," Robotics and Autonomous Systems, vol. 61, no. 5, pp. 517-544, 2013.
[2] G. Alici, "Softer is Harder:What Differentiates Soft Robotics from Hard Robotics?," MRS Advances, vol. 3, no. 28, pp. 1557-1568, 2018.
[3] V. Trappe, V. Prasad, L. Cipelletti, P. N. Segre and D. A. Weitz, "Jamming phase diagram for attractive particles," Nature, vol. 411, no. 6839, p. 772, 2001.
[4] K. Lu, E. E. Brodsky and H. P. Kavehpour, "A thermodynamic unification of jamming," Nature Physics, vol. 4, no. 5, p. 404, 2008.
[5] A. J. Liu and S. R. Nagel, "Nonlinear dynamics: Jamming is not just cool any more," Nature, vol. 396, no. 6706, p. 21, 1998.
[6] E. Brown, N. Rodenberg, J. Amend, A. Mozeika, E. Steltz, M. R. Zakin, H. Lipson and H. M. Jaeger, "Universal robotic gripper based on the jamming of granular material," Proceedings of the National Academy of Sciences, vol. 107, no. 44, pp. 18809-18814, 2010.
[7] J. R. Amend, E. Brown, N. Rodenberg, H. M. Jaeger and H. Lipson, "A Positive Pressure Universal Gripper Based on the Jamming of Granular Material," IEEE Transactions on Robotics, vol. 28, no. 2, pp. 341-350, 2012.
[8] N. G. Cheng, M. B. Lobovsky, S. J. Keating, A. M. Setapen, K. I. Gero, A. E. Hosoi and K. D. Iagnemma, "Design and analysis of a robust, low-cost, highly articulated manipulator enabled by jamming of granular media," in Robotics and Automation (ICRA), 2012 IEEE International Conference on, Saint Paul, Minnesota, Usa, 2012.
[9] S. Reitelshöfer, C. Ramer, D. Gräf, F. Matern and J. Franke, "Combining a collaborative robot and a lightweight Jamming-Gripper to realize an intuitively to use and flexible co-worker," in System Integration (SII), 2014 IEEE/SICE International Symposium on, 1-5, 2014.
[10] E. Steltz, A. Mozeika, J. Rembisz, N. Corson and H. M. Jaeger, "Jamming as an enabling technology for soft robotics," in Electroactive Polymer Actuators and Devices (EAPAD) 2010, 2012.
[11] M. Ciocarlie and P. Allen, "Data-driven optimization for underactuated robotic hands," in Robotics and Automation (ICRA), 2010 IEEE International Conference on, Anchorage, Alaska, USA, 2010.
[12] R. Deimel and O. Brock, "A Novel Type of Compliant, Underactuated Robotic Hand for Dextrous Grasping," The International Journal of Robotics Research, vol. 35, no. 1-3, pp. 161-185, 2016.
[13] C. Gosselin, F. Pelletier and T. Laliberte, "An anthropomorphic underactuated robotic hand with 15 dofs and a single actuator," in Robotics and Automation, 2008. ICRA 2008. IEEE International Conference on, Pasadena, CA, USA, 2008.
[14] M. Ciocarlie, A. Miller and P. Allen, "Grasp analysis using deformable fingers," in Intelligent Robots and Systems, 2005.(IROS 2005). 2005 IEEE/RSJ International Conference on, 2005.
[15] L. U. Odhner, L. P. Jentoft, M. R. Claffee, N. Corson, Y. Tenzer, R.
R. Ma, M. Buehler, R. Kohout, R. D. Howe and A. M. Dollar, "A compliant, underactuated hand for robust manipulation," The International Journal of Robotics Research, vol. 5, no. 33, pp. 736-752, 2014.
[16] K. Mizushima, T. Oku, Y. Suzuki, T. Tsuji and T. Watanabe, "Multi-fingered robotic hand based on hybrid mechanism of tendon-driven and jamming transition," in 2018 IEEE International Conference on Soft Robotics (RoboSoft), 2018.
[17] R. R. Ma, A. Spiers and A. M. Dollar, "M 2 Gripper: Extending the Dexterity of a Simple, Underactuated Gripper," in Advances in reconfigurable mechanisms and robots II, Springer, 2016, pp. 795-805.
[18] B. Rubinger, M. Brousseau, J. Lymer, C. M. Gosselin, T. Laliberte and J.-C. Piedboeuf, "A novel robotic hand-SARAH for operations on the international space station," in Proceeding of the ASTRA 2002 Workshop, Noordwijk, The Netherlands, 2002.
[19] Y. Wei, Y. Chen, T. Ren, Q. Chen, C. Yan, Y. Yang and Y. Li, "A Novel, Variable Stiffness Robotic Gripper Based on Integrated Soft Actuating and Particle Jamming," Soft Robotics, vol. 3, 07 2016.
[20] Y. Yang, Y. Chen, Y. Li, M. Z. Chen and Y. Wei, "Bioinspired robotic fingers based on pneumatic actuator and 3D printing of smart material," Soft Robotics, vol. 4, no. 2, pp. 147-162, 2017.
[21] M. van Hecke, "Jamming of soft particles: geometry, mechanics, scaling and isostaticity," Journal of Physics: Condensed Matter, vol. 22, no. 3, p. 033101, 2009.
[22] S. Shirafuji, S. Ikemoto and K. Hosoda, "Development of a tendon-driven robotic finger for an anthropomorphic robotic hand," The International Journal of Robotics Research, vol. 33, no. 5, pp. 677-693, 2014.
[23] J. Lai, "Moldflow Material Testing Report MAT2238-NatureWorks PLA," Moldflow, Victoria, Australia, 2007.
[24] J. Torres, J. Cotelo, J. Karl and A. P. Gordon, "Mechanical Property Optimization of FDM PLA in Shear with Multiple Objectives," Jom, vol. 67, no. 5, pp. 1183-1193, 2015.
[25] X. He, M. Qu and X. Shi, "Damping Properties of Ethylene-Vinyl Acetate Rubber/Polylactic Acid Blends," Journal of Materials Science and Chemical Engineering, vol. 4, no. 03, p. 15, 03 23 2016.
[26] "Thermal expansion coefficient determination of polylactic acid using digital image correlation," in E3S Web of Conferences, 2018.
[27] T. S. Majmudar, M. Sperl, S. Luding and R. P. Behringer, "Jamming Transition in Granular Systems," Physical review letters, vol. 98, no. 5, p. 058001, 2007.
[28] T. Inoue and S. Hirai, "Elastic model of deformable fingertip for soft-fingered manipulation," IEEE Trans. Robotics, vol. 22, no. 6, pp. 1273-1279, 2006.
[29] T. Inoue and S. Hirai, "How Hemispherical Soft Fingertips Enhance Dexterity in Grasping and Manipulation," in Proc. of the 2007 IEEE Int. Conf. on Robotics and Biomimetics, Dec, Kusatsu, Shiga, 2007.

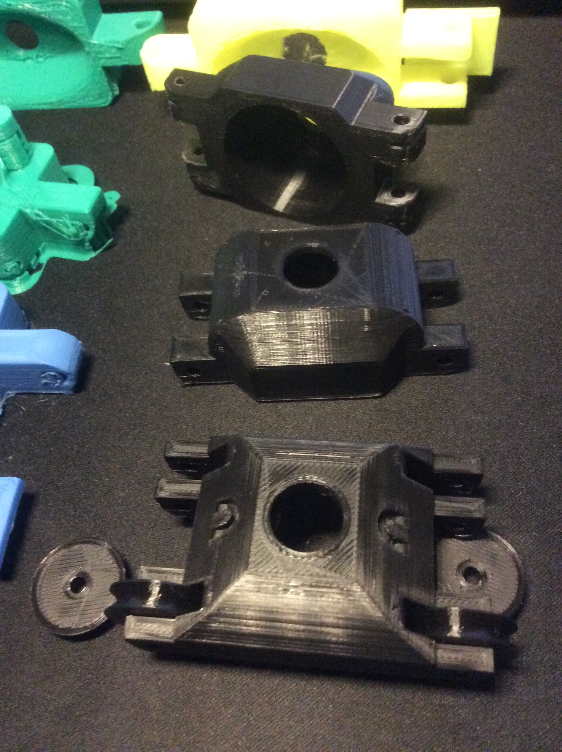
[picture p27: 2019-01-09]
Pictures/Final Design Back.JPG

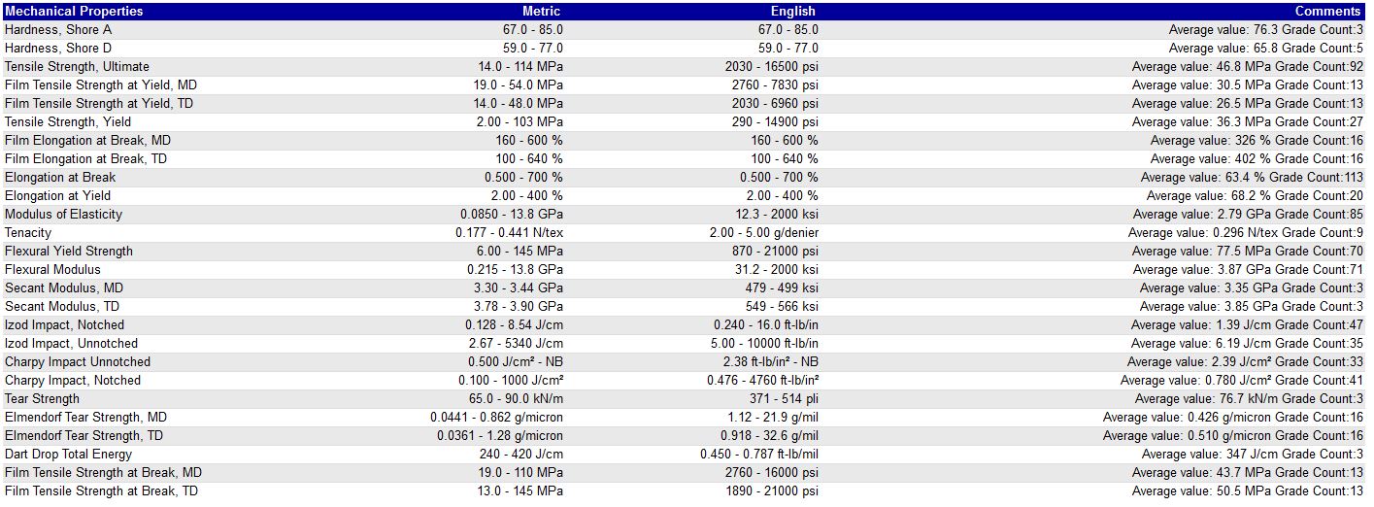
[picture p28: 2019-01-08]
Pictures/PLA Mechanical Properties, Matweb.JPG

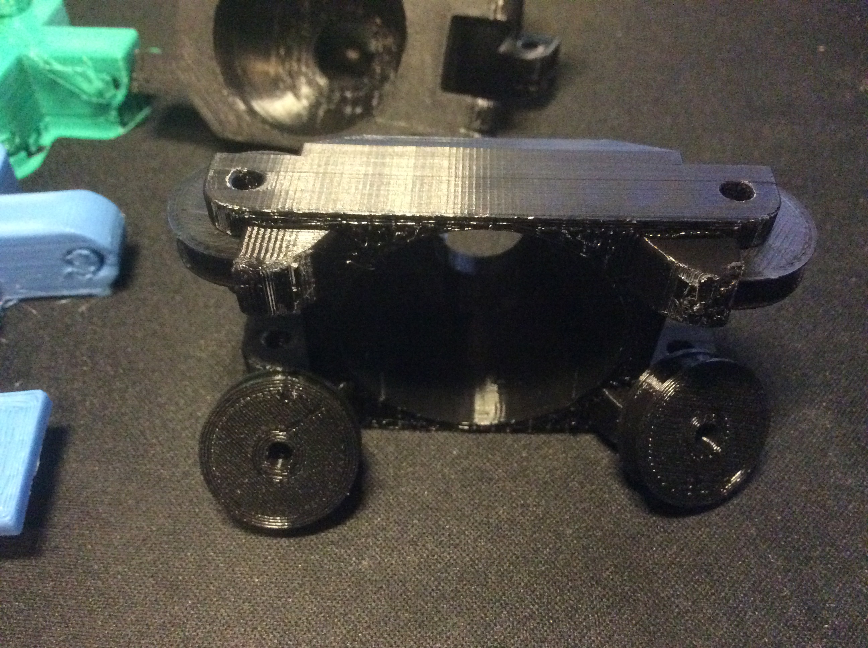
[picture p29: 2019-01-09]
Pictures/Final Design.JPG

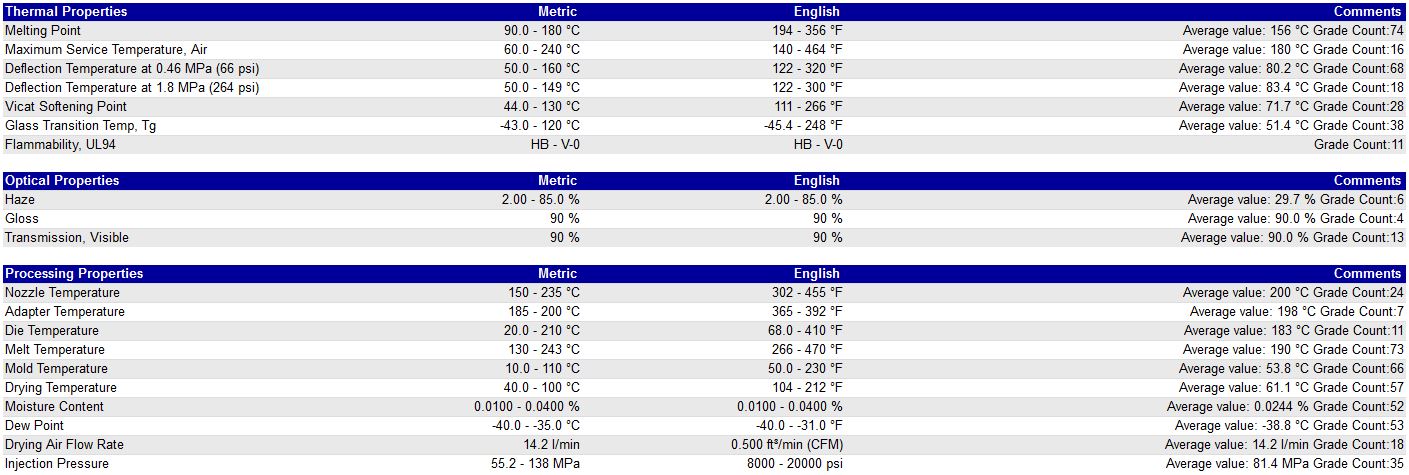
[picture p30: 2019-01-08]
Pictures/PLA Thermal, Optical, Processing Properties, Matweb.JPG

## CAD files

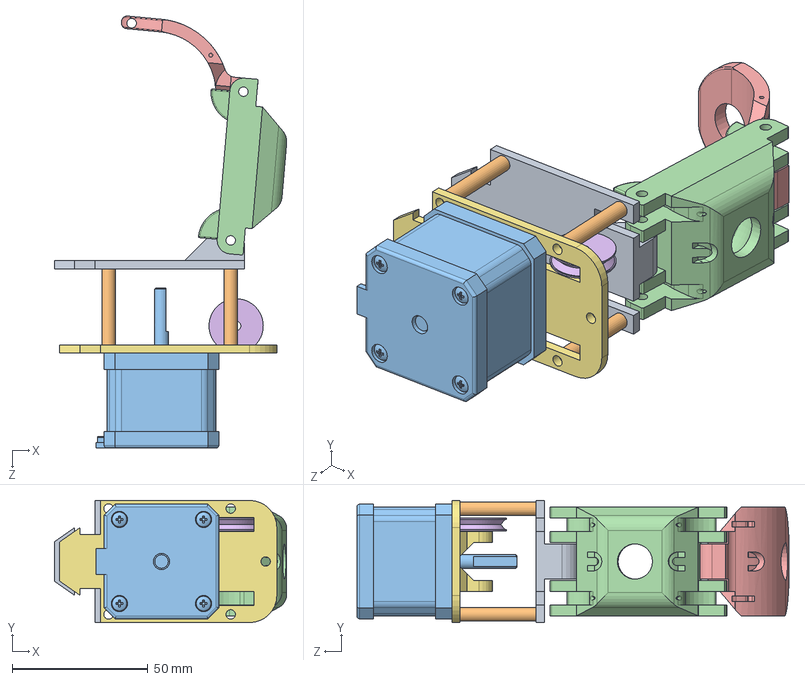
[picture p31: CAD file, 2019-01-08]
CAD/Iteration 4 CAD/Assemblies/Assembly Attempt.SLDASM
85.6 x 45.0 x 159.2 mm
BaseA_1_3
Spacer x 4
NEMA 17
Mid1_6
EndLink1_5
Pivot
BaseB_1_2

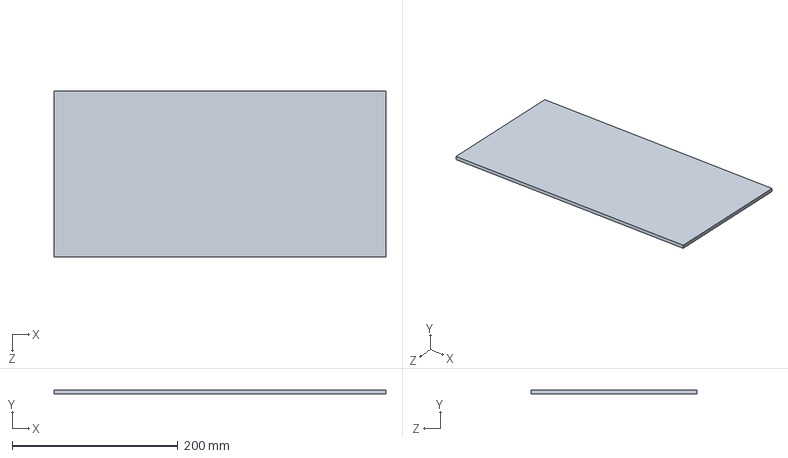
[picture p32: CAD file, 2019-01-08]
CAD/Iteration 4 CAD/Pneumatics/Sample Base for Assembly.SLDPRT
400.0 x 5.00 x 200.0 mm

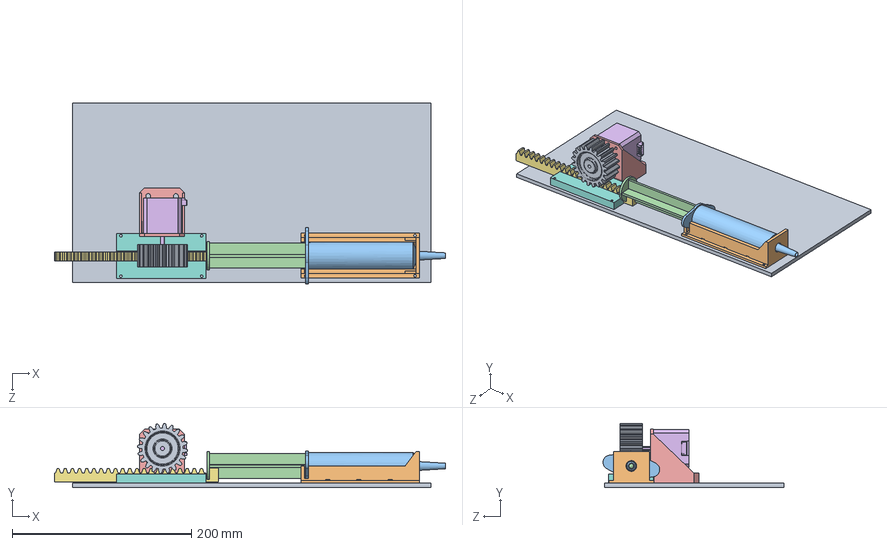
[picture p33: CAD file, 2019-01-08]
CAD/Iteration 4 CAD/Pneumatics/Pneumatics Assembly.SLDASM
436.1 x 71.4 x 201.9 mm
base
holder 1
syrp1
syrp2
NEMA 17 Motor Mount Plate
nema 17 SLDPRT
rack
rail run
gear_20

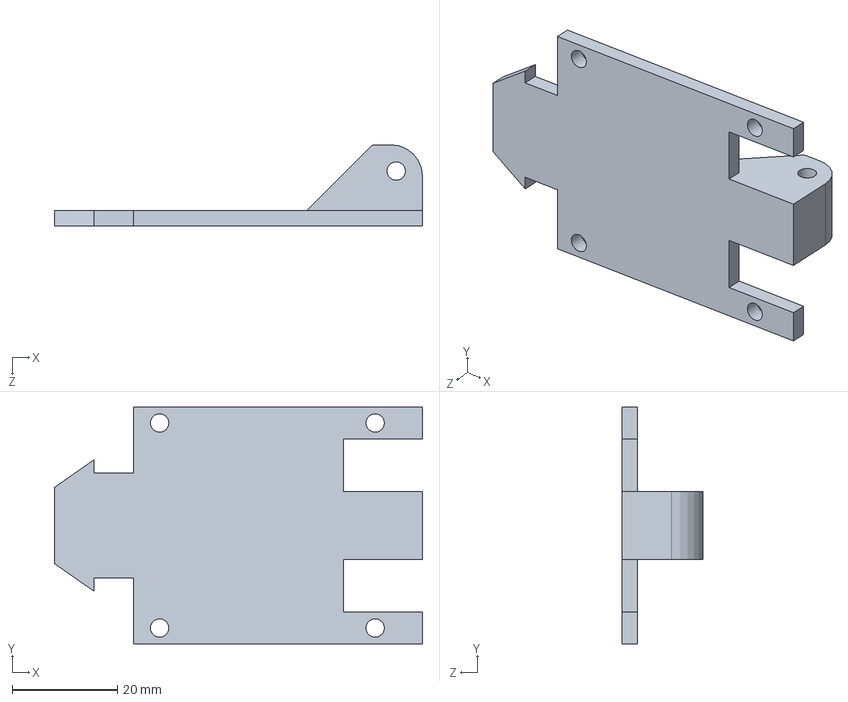
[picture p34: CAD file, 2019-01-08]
CAD/Iteration 4 CAD/Base/BaseA_1_4.SLDPRT
70.0 x 45.0 x 15.5 mm

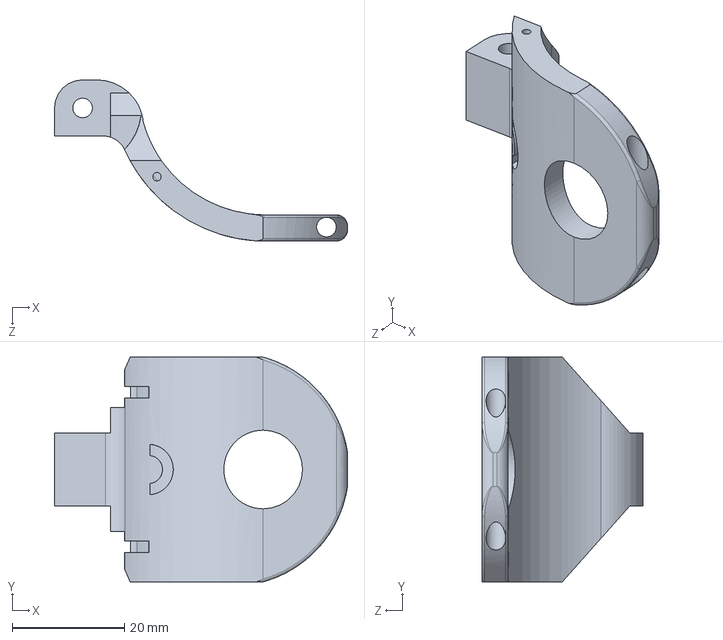
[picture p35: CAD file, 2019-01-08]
CAD/Iteration 4 CAD/Endlink/EndLink1_4.SLDPRT
52.1 x 40.0 x 28.7 mm

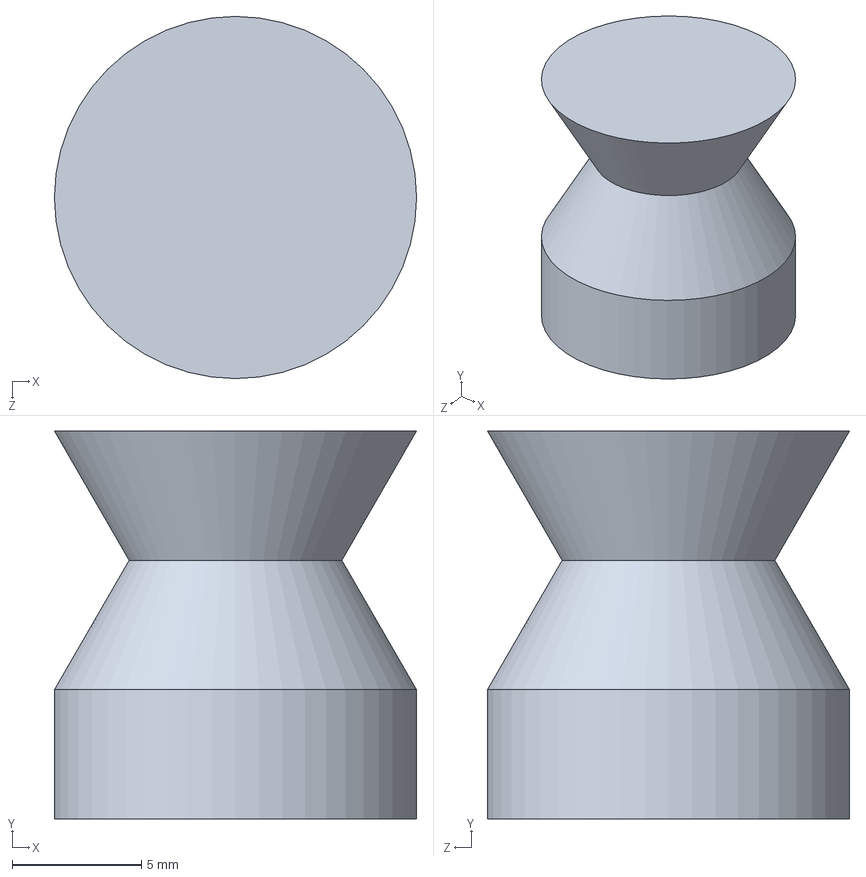
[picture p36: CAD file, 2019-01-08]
CAD/Iteration 4 CAD/Initial Digit Designs/spindle.SLDPRT
14.0 x 15.0 x 14.0 mm

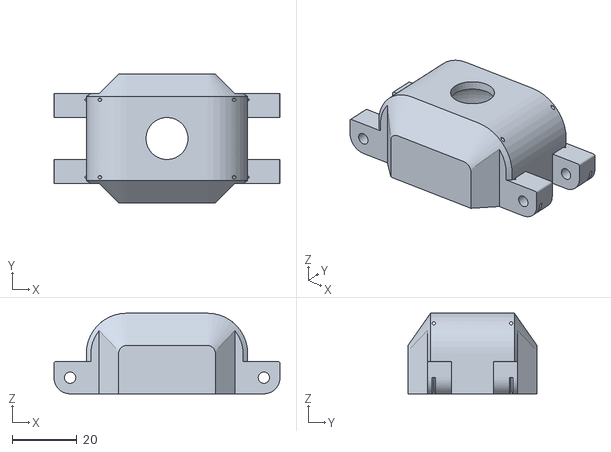
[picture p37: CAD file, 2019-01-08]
CAD/Iteration 4 CAD/Midlink/Midlink1_2_Print_Att.STL
70.0 x 40.0 x 25.0

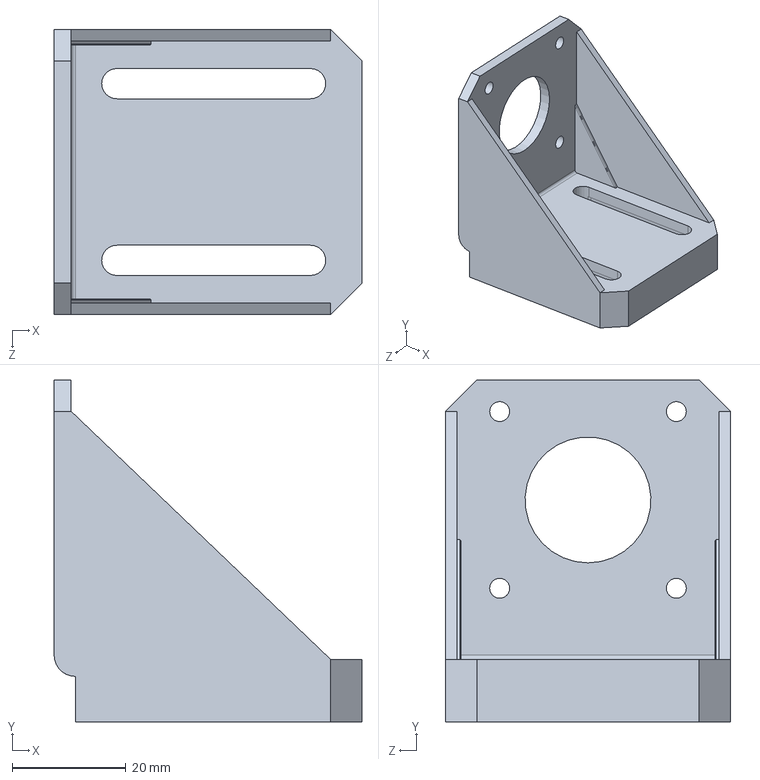
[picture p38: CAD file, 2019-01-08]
CAD/Iteration 4 CAD/Pneumatics/Motor Mount.SLDPRT
54.0 x 60.0 x 50.0 mm

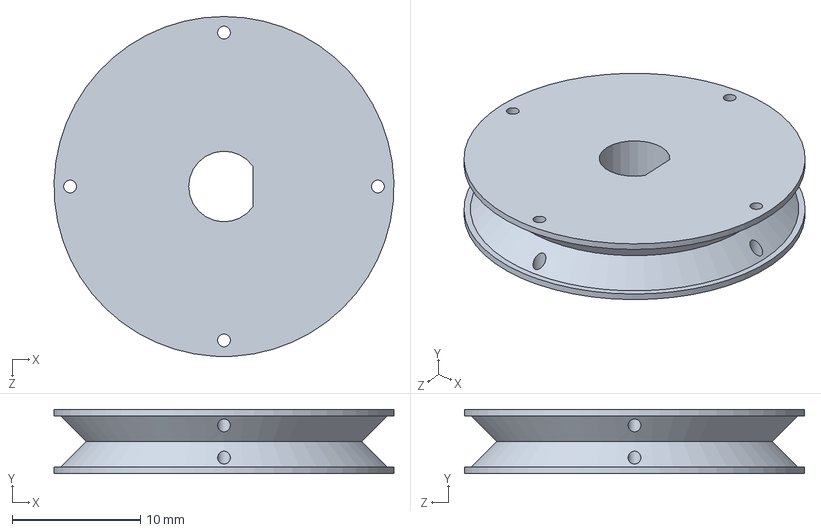
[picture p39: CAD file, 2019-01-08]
CAD/Iteration 4 CAD/Structural/Base Pivot.SLDPRT
26.5 x 5.00 x 26.5 mm

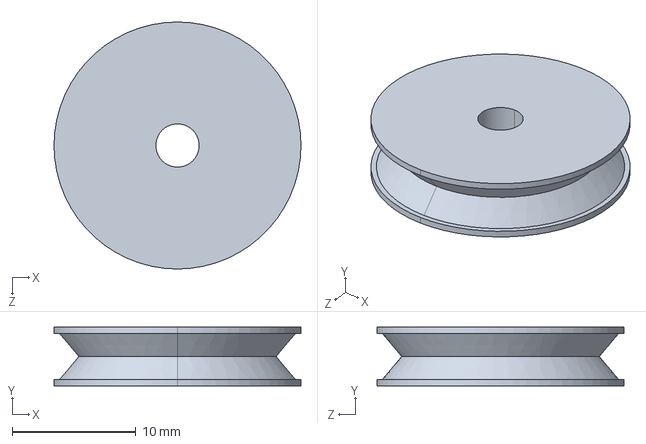
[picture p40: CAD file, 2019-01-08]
CAD/Shareable CAD Files/Pivot.STEP
20.0 x 4.75 x 20.0 mm

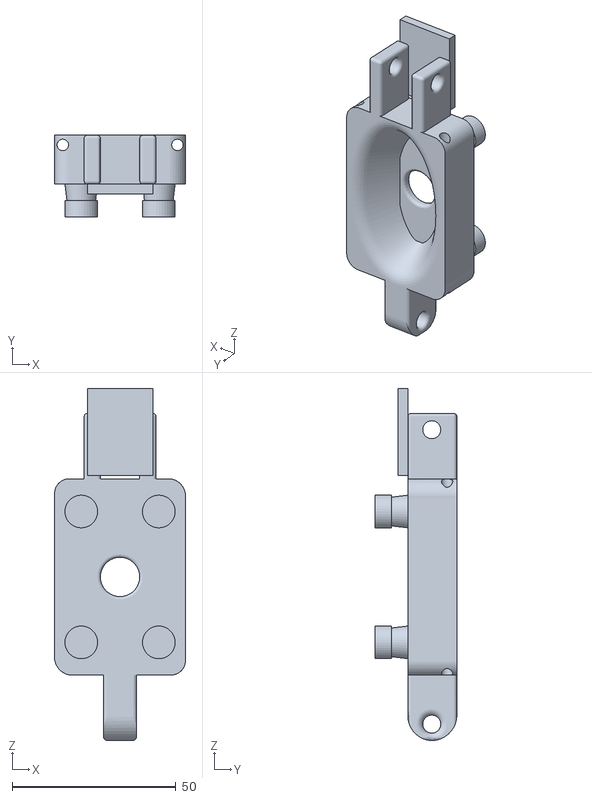
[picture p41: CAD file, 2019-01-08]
STLs/Prints/Prototyping/Digit 2v4.STL
40.1 x 25.0 x 107.6

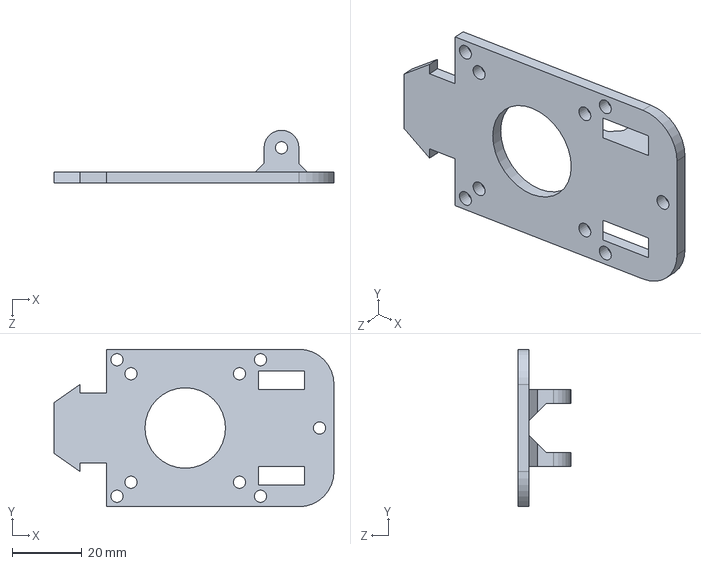
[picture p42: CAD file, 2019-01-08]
CAD/Iteration 4 CAD/Base/BaseB_1_3.SLDPRT
80.0 x 45.0 x 15.0 mm

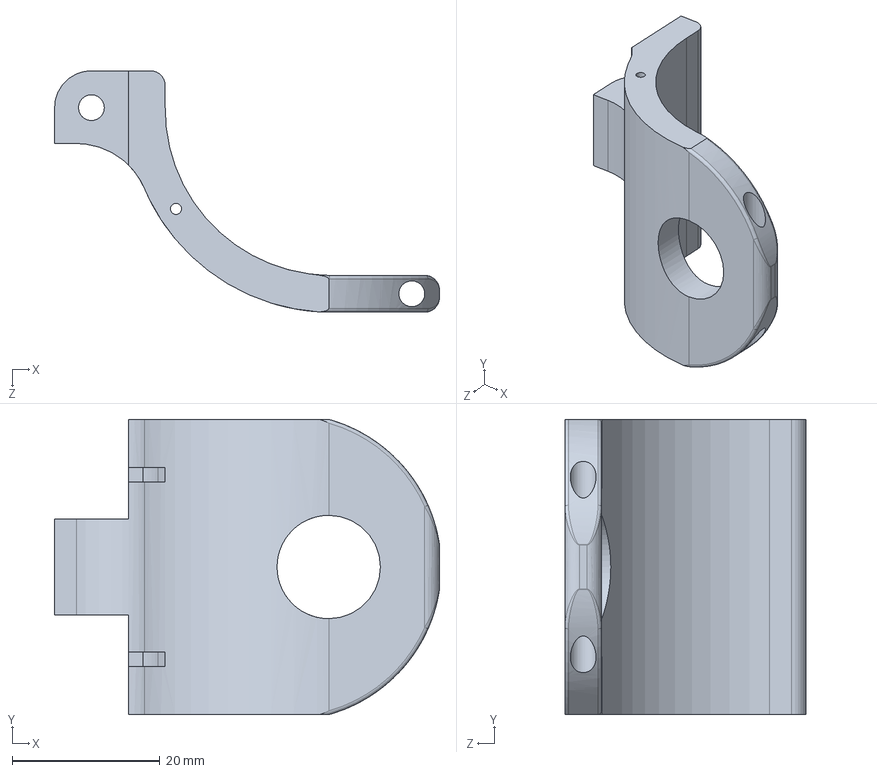
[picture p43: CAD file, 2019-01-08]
CAD/Iteration 4 CAD/Endlink/EndLink1_1.SLDPRT
52.1 x 40.0 x 32.7 mm

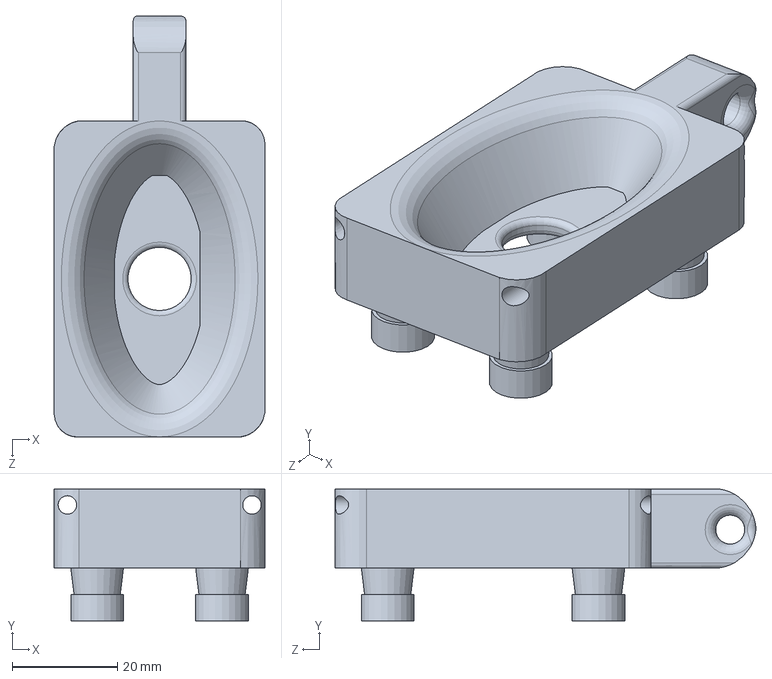
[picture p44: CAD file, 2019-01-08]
CAD/Iteration 4 CAD/Initial Digit Designs/Digit 1.SLDPRT
40.0 x 25.0 x 79.9 mm

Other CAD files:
STLs/Prints/Base Pivot.STL
Test_data/FEA/Solidworks Files/Digit2 Fat.SLDPRT
CAD/Iteration 4 CAD/Midlink/1_4.SLDPRT
CAD/Iteration 4 CAD/Pneumatics/Syringe P1.SLDPRT
CAD/Iteration 4 CAD/Base/BaseA_1_1.SLDPRT
CAD/Iteration 4 CAD/Base/BaseA_1_2.SLDPRT
CAD/Iteration 4 CAD/Base/BaseA_1_3.SLDPRT
CAD/Iteration 4 CAD/Base/BaseB_1_1.SLDPRT
CAD/Iteration 4 CAD/Base/BaseB_1_2.SLDPRT
CAD/Iteration 4 CAD/Endlink/End Link.SLDPRT
CAD/Iteration 4 CAD/Endlink/End Link_Print.STL
CAD/Iteration 4 CAD/Endlink/EndLink1_1.STL
CAD/Iteration 4 CAD/Endlink/EndLink1_2.SLDPRT
CAD/Iteration 4 CAD/Endlink/EndLink1_3.SLDPRT
CAD/Iteration 4 CAD/Endlink/EndLink1_4.STL
CAD/Iteration 4 CAD/Endlink/EndLink1_5.SLDPRT
CAD/Iteration 4 CAD/Initial Digit Designs/Digit 2.SLDPRT
CAD/Iteration 4 CAD/Midlink/1.2.SLDPRT
CAD/Iteration 4 CAD/Midlink/1_3.SLDPRT
CAD/Iteration 4 CAD/Midlink/1_3.STL
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

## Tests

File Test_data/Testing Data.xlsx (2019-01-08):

Shape | Vol1 | Force1 | Vol2 | Force2 | Vol3 | Force3 | V4 | F4 | FA
Printside | 10 | 3 | 10 | 4 | 10 | 3 | 17 | 19 | 3.3
0 Edges | 10 | 4 | 10 | 9 | 15 | 14 | 15 | 11 | 11.3
1 Edge | 10 | 14 | 15 | 17 | 10 | 12 | 10 | 12 | 12.7
2 Edges | 10 | 5 | 15 | 13 | 14 | 12 | 15 | 15 | 10.0
Hollow | 20 | 22 | 10 | 1 | 10 | 18 | 15 | 14 | 18.0
spring | 25 | 10 | 15 | 5 | 20 | 6 | 10 | 1 | 7.0
screw | 20 | 22 | 10 | 1 | 15 | 6 | 10 | 1 | 2.7
button | 15 | 7 | 15 | 9 | 15 | 10 | 15 | 12 | 8.7
6mm Nut | 15 | 0 | 15 | 0 | 15 | 0 | 15 | 1 | 0.0
Cotton | 15 | 0 | 15 | 1 | 15 | 1 | 15 | 2 | 0.7
Shape : Hollow |  | Vol | Force1 | F2 | F3 | FA
 |  | 10 | 5 | 4 | 4 | 4.333333333
 |  | 20 | 5 | 7 | 7 | 6.333333333
 |  | 30 | 10 | 9 | 9 | 9.333333333
 |  | 40 | 14 | 14 | 13 | 13.66666667
 |  | 50 | 17 | 19 | 21 | 19

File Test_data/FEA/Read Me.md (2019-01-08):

Using Solidworks Simualtions, these files contain FEA Data used in the rapid prototyping process.

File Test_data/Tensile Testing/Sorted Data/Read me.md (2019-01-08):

Using a tensile testing machine, data in this/these folders was generated.

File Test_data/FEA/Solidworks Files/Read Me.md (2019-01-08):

Using Solidworks Simualtions, these files contain FEA Data used in the rapid prototyping process.

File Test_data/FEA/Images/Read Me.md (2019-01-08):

Using Solidworks Simualtions, these files contain FEA Images

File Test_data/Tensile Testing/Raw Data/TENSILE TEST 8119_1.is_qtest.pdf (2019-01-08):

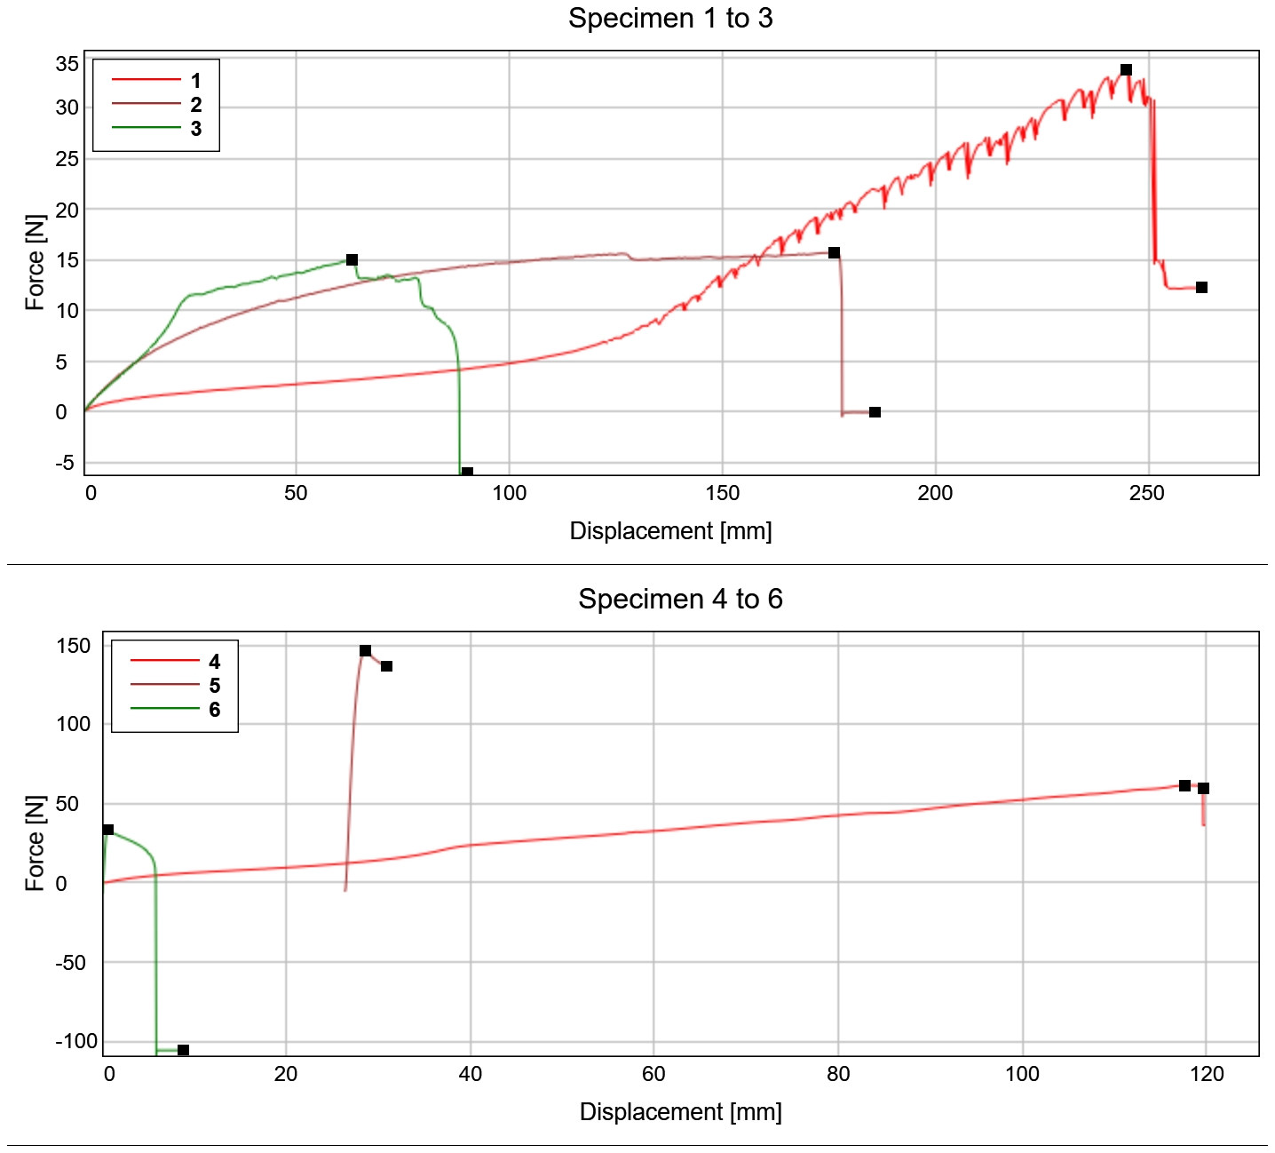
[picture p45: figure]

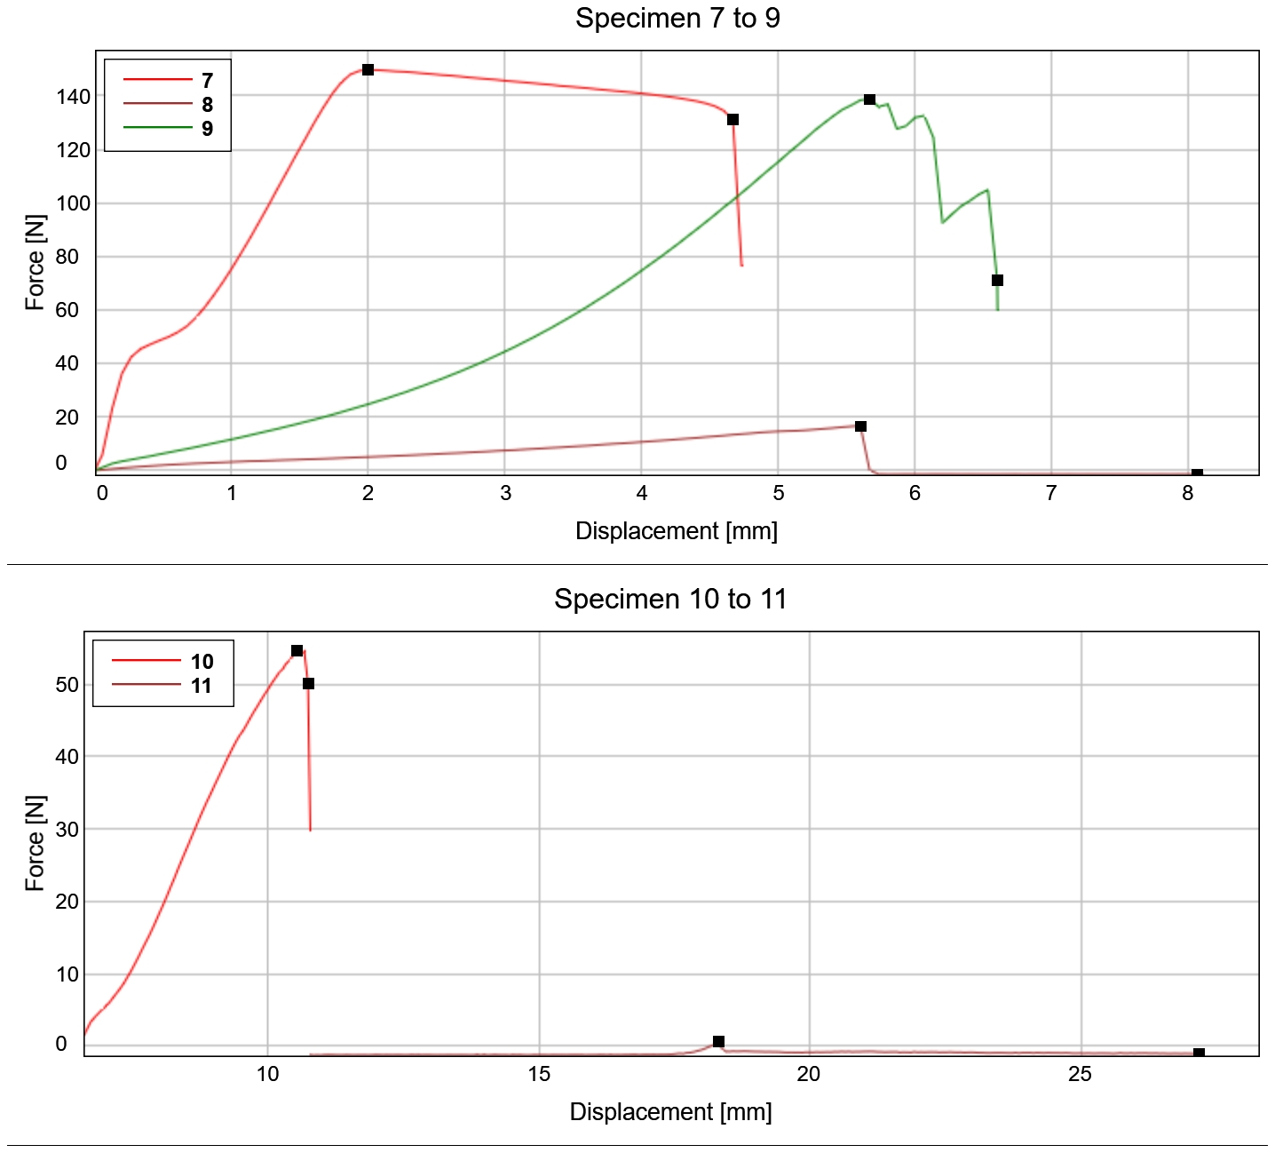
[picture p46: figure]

| Maximum Force [kN] | Displacement at Maximum Force [mm] | Maximum Displacement [mm] | Force at Break (Standard) [kN]
1 | 0.03 | 245.10 | 262.81 | 0.01
2 | 0.02 | 176.33 | 185.99 | 0.00
3 | 0.01 | 63.00 | 90.01 | -0.01
4 | 0.06 | 117.60 | 119.63 | 0.06
5 | 0.15 | 28.59 | 30.87 | 0.14
6 | 0.03 | 0.60 | 8.81 | -0.11
7 | 0.15 | 2.00 | 4.73 | 0.13
8 | 0.02 | 5.60 | 8.11 | 0.00

| Maximum Force [kN] | Displacement at Maximum Force [mm] | Maximum Displacement [mm] | Force at Break (Standard) [kN]
9 | 0.14 | 5.67 | 6.60 | 0.07
10 | 0.05 | 10.54 | 10.78 | 0.05
11 | 0.00 | 18.32 | 27.25 | 0.00
| Specimen text input
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
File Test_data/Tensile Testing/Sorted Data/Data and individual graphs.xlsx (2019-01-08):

Elastic 2mm |  |  | NinjaFlex - Failed Attempt 1 |  |  | NinjaFlex - Failed Attempt 2 |  |  | NinjaFlex - Successful Attempt |  |  | PLA |  |  | PLA |  |  | Fishing Line |  |  | Nylon Break 1 |  |  | Nylon Break 2 |  |  | Nylon break 3
Time | Displacement | Force | Time | Displacement | Force | Time | Displacement | Force | Time | Displacement | Force | Time | Displacement | Force | Time | Displacement | Force | Time | Displacement | Force | Time | Displacement | Force | Time | Displacement | Force | Time | Displacement | Force
(s) | (mm) | (kN) | (s) | (mm) | (kN) | (s) | (mm) | (kN) | (s) | (mm) | (kN) | (s) | (mm) | (kN) | (s) | (mm) | (kN) | (s) | (mm) | (kN) | (s) | (mm) | (kN) | (s) | (mm) | (kN) | (s) | (mm) | (kN)
0 | 0 | -0.0001 | 0 | 0 | 0 | 0 | 0.0001 | 0 | 0 | 0 | 0 | 0 | 0 | -0.007 | 0 | 0 | 0.0003 | 0 | 0 | -0.0001 | 0 | 0 | 0 | 0 | 6.6041 | 0.0014 | 0 | 10.7815 | -0.0012
0.1 | 0.0225 | 0 | 0.1 | 0.0681 | 0 | 0.1 | 0.0704 | -0.0001 | 0.1 | 0.1095 | 0 | 0.1 | 0.05 | -0.0036 | 0.1 | 0.0511 | 0.0056 | 0.1 | 0.0524 | 0.0001 | 0.1 | 0.052 | 0.001 | 0.1 | 6.6548 | 0.0022 | 0.1 | 10.8327 | -0.0013
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

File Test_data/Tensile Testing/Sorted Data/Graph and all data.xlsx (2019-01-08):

Elastic 2mm |  |  | NinjaFlex |  |  | NinjaFlex |  |  | NinjaFlex |  |  | PLA |  |  | PLA |  |  | Fishing Line |  |  | Nylon Break 1 |  |  | Nylon Break 2 |  |  | Nylon break 3
Time | Displacement | Force | Time | Displacement | Force | Time | Displacement | Force | Time | Displacement | Force | Time | Displacement | Force | Time | Displacement | Force | Time | Displacement | Force | Time | Displacement | Force | Time | Displacement | Force | Time | Displacement | Force
(s) | (mm) | (kN) | (s) | (mm) | (kN) | (s) | (mm) | (kN) | (s) | (mm) | (kN) | (s) | (mm) | (kN) | (s) | (mm) | (kN) | (s) | (mm) | (kN) | (s) | (mm) | (kN) | (s) | (mm) | (kN) | (s) | (mm) | (kN)
0 | 0 | -0.0001 | 0 | 0 | 0 | 0 | 0.0001 | 0 | 0 | 0 | 0 | 0 | 0 | -0.007 | 0 | 0 | 0.0003 | 0 | 0 | -0.0001 | 0 | 0 | 0 | 0 | 6.6041 | 0.0014 | 0 | 10.7815 | -0.0012
0.1 | 0.0225 | 0 | 0.1 | 0.0681 | 0 | 0.1 | 0.0704 | -0.0001 | 0.1 | 0.1095 | 0 | 0.1 | 0.05 | -0.0036 | 0.1 | 0.0511 | 0.0056 | 0.1 | 0.0524 | 0.0001 | 0.1 | 0.052 | 0.001 | 0.1 | 6.6548 | 0.0022 | 0.1 | 10.8327 | -0.0013
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

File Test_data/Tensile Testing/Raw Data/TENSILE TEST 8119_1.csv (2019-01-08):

Results Table 1
 | Maximum Force | Displacement at Maximum Force | Maximum Displacement | Force at Break (Standard) | Specimen text input
 | (kN) | (mm) | (mm) | (kN)
1 | 0.12 | 16.71 | 16.71 | 0.12
2 | 0.18 | 15.52 | 15.55 | 0.18
3 | 0.06 | 22.83 | 22.91 | 0.06
4 | 0.06 | 9.37 | 9.39 | 0.06
5 | 0.04 | 28.00 | 36.63 | 0.00
Results Table 2

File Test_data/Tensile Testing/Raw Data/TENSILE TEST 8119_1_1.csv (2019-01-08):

Elastic 2mm |  |  | NinjaFlex |  |  | NinjaFlex |  |  | NinjaFlex |  |  | PLA |  |  | PLA |  |  | Fishing Line |  |  | Nylon Break 1 |  |  | Nylon Break 2 |  |  | Nylon break 3
Time | Displacement | Force | Time | Displacement | Force | Time | Displacement | Force | Time | Displacement | Force | Time | Displacement | Force | Time | Displacement | Force | Time | Displacement | Force | Time | Displacement | Force | Time | Displacement | Force | Time | Displacement | Force
(s) | (mm) | (kN) | (s) | (mm) | (kN) | (s) | (mm) | (kN) | (s) | (mm) | (kN) | (s) | (mm) | (kN) | (s) | (mm) | (kN) | (s) | (mm) | (kN) | (s) | (mm) | (kN) | (s) | (mm) | (kN) | (s) | (mm) | (kN)
0 | 0 | -0.0001 | 0 | 0 | 0 | 0 | 0.0001 | 0 | 0 | 0 | 0 | 0 | 0 | -0.007 | 0 | 0 | 0.0003 | 0 | 0 | -0.0001 | 0 | 0 | 0 | 0 | 6.6041 | 0.0014 | 0 | 10.7815 | -0.0012
0.1 | 0.0225 | 0 | 0.1 | 0.0681 | 0 | 0.1 | 0.0704 | -0.0001 | 0.1 | 0.1095 | 0 | 0.1 | 0.05 | -0.0036 | 0.1 | 0.0511 | 0.0056 | 0.1 | 0.0524 | 0.0001 | 0.1 | 0.052 | 0.001 | 0.1 | 6.6548 | 0.0022 | 0.1 | 10.8327 | -0.0013
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

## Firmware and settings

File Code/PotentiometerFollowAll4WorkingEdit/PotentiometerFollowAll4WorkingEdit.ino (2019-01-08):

/*
   StepperCodeIteration1
   Written by DjTilley for ROCO504
   Used to control a soft robotic gripper
*/

#include <AccelStepper.h>

#define PotPos1 (A0)
#define PotPos2 (A1)
#define PotPos3 (A2)
#define PotPos4 (A3)

#define MOTOR_SCALING 2                                                                       8

AccelStepper NemStp1(AccelStepper::DRIVER, 3, 4);
AccelStepper NemStp2(AccelStepper::DRIVER, 5, 6);
AccelStepper NemStp3(AccelStepper::DRIVER, 7, 8);
AccelStepper NemStp4(AccelStepper::DRIVER, 9, 10);

int Pval1 = 0;
int previous1 = 0;
int long Pnewval1 = 0;

int Pval2 = 0;
int previous2 = 0;
int long Pnewval2 = 0;

int Pval3 = 0;
int previous3 = 0;
int long Pnewval3 = 0;

int Pval4 = 0;
int previous4 = 0;
int long Pnewval4 = 0;

void setup()
{
  Serial.begin(9600);
  NemStp1.setMaxSpeed(3500);
  NemStp1.setAcceleration(3500);
  NemStp2.setMaxSpeed(3500);
  NemStp2.setAcceleration(3500);
  NemStp3.setMaxSpeed(3500);
  NemStp3.setAcceleration(3500);
  NemStp4.setMaxSpeed(3500);
  NemStp4.setAcceleration(3500);
  pinMode(PotPos1, INPUT);
  pinMode(PotPos2, INPUT);
  pinMode(PotPos3, INPUT);
  pinMode(PotPos4, INPUT);
}

void loop()
{
  Pval1 = analogRead(PotPos1);
  if ((Pval1 > previous1 + 6) || (Pval1 < previous1 - 6)) {
    Pnewval1 = map(Pval1, 0, 1023, 0, ( 200 * MOTOR_SCALING));
    NemStp1.runToNewPosition(-Pnewval1);
    previous1 = Pval1;
  }

  Pval2 = analogRead(PotPos2);
  if ((Pval2 > previous2 + 6) || (Pval2 < previous2 - 6)) {
    Pnewval2 = map(Pval2, 0, 1023, 0, ( 200 * MOTOR_SCALING));
    NemStp2.runToNewPosition(-Pnewval2);
    previous2 = Pval2;
  }

  Pval3 = analogRead(PotPos3);
  if ((Pval3 > previous3 + 6) || (Pval3 < previous3 - 6)) {
    Pnewval3 = map(Pval3, 0, 1023, 0, ( 200 * MOTOR_SCALING));
    NemStp3.runToNewPosition(-Pnewval3);
    previous3 = Pval3;
  }

  Pval4 = analogRead(PotPos4);
  if ((Pval4 > previous4 + 6) || (Pval4 < previous4 - 6)) {
    Pnewval4 = map(Pval4, 0, 1023, 0, ( 200 * MOTOR_SCALING));
    NemStp4.runToNewPosition(-Pnewval4);
    previous4 = Pval4;
  }

}

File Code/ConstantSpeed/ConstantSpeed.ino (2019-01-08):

/*
   StepperCodeIteration1
   Written by DjTilley for ROCO504
   Used to control a soft robotic gripper
*/

#include <AccelStepper.h>

#define PotPos1 (A0)

AccelStepper NemStp1(AccelStepper::DRIVER, 3, 4);
AccelStepper NemStp2(AccelStepper::DRIVER, 5, 6);
AccelStepper NemStp3(AccelStepper::DRIVER, 7, 8);
AccelStepper NemStp4(AccelStepper::DRIVER, 9, 10);

void setup()
{
  Serial.begin(9600);
  NemStp1.setMaxSpeed(1000);
  NemStp1.setSpeed(200);
  NemStp2.setMaxSpeed(1000);
  NemStp2.setSpeed(200);
  NemStp3.setMaxSpeed(1000);
  NemStp3.setSpeed(200);
  NemStp4.setMaxSpeed(1000);
  NemStp4.setSpeed(200);
}

void loop()
{
  NemStp1.runSpeed();
  NemStp2.runSpeed();
  NemStp3.runSpeed();
  NemStp4.runSpeed();
}

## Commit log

2019-01-08 Create STL Description
2019-01-08 Delete BaseA_1_3.STL
    Upgraded
    [BaseA_1_3.STL]
2019-01-08 Delete BaseB_1_2.STL
    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
    [BaseB_1_2.STL]
2019-01-08 Delete Nema 17.SLDPRT
    Unsure of Licensing
    [Nema 17.SLDPRT]
2019-01-08 Delete Digit 2v4.STL
    moving to different directory
    [Digit 2v4.STL]
2019-01-08 Delete Digit 2v2.STL
    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
    [Digit 2v2.STL]
2019-01-08 Delete Digit 2 v3.STL
    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
    [Digit 2 v3.STL]
2019-01-08 Delete Digit 1v4.STL
    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
    [Digit 1v4.STL]
2019-01-08 Delete Digit 1.STL
    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
    [Digit 1.STL]
2019-01-08 Delete Digit 1v2.STL
    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
    [Digit 1v2.STL]
2019-01-08 Delete Digit 2.STL
    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
    [Digit 2.STL]
2019-01-08 Delete Digit 1 v3.STL
    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
    [Digit 1 v3.STL]
2019-01-08 Add files via upload
    Updated directory
    [Digit 1 v3.STL, Digit 1.STL, Digit 1v2.STL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]
